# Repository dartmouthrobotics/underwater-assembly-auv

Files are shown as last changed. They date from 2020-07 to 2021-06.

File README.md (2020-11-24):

# Dartmouth Droplet AUV
Repository containing parts list and CAD files to retrofit a BlueROV2 for improved autonomous operation. The starting point would be a BlueROV2 heavy. A CAD file of the build is available [here](https://www.dropbox.com/s/99sjkslvtko1nd0/Electronics.igs?dl=0). Note that the front mounting plate is different than what is in that CAD file. I was experimenting with adding fans for camera cooling. What I use now in the robot is represented in the dxf file below.

The DXF files are usable as laser cutting patterns. The files `Electronics Tray Body.dxf`, `Electronics Tray Body.dxf`, and `rear electronics tray mount.dxf` are cut from 4.9mm delrin plastic from ponoko.com

The file `Camera Mount.dxf` is cut from 3.2mm black delrin from ponoko.

The file `FCU Mount.dxf` is cut from 2mm aerospace aluminum from send cut send.

The hardware for assembling the components comes from mcmaster-carr and allied electronics (for the mounting brackets). See the packing lists for both of those orders for details on the components.

# Electronics

ESCs: 2x DALRC rocket 50a from [here](https://www.getfpv.com/dalrc-rocket-50a-3-6s-blheli-32-4-in-1-esc.html). You also need another FCU to configure the ESCs. We use the DALRC f722 dual from [here](https://www.banggood.com/DALRC-F722-DUAL-STM32F722RGT6-F7-Flight-Controller-MPU6000-and-ICM20602-Built-in-OSD-for-RC-Drone-p-1346923.html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)

Main computer: UpBoard UpSquared [here](https://up-board.org/upsquared/specifications/). We use the 8GB ram quad core model
Main computer addons:
  * UpSquared wifi kit [here](https://up-shop.org/m-2-2230-wifi-kit-wifi-802-11-ac-2t2r-for-up-squared-metal-chassis.html) used to connect to the robot when it is on the surface
  * SSD for the upboard. We use [this one](https://www.amazon.com/gp/product/B07GZLJD5R/ref=ppx_yo_dt_b_search_asin_title?ie=UTF8&psc=1)
  * Tiny USB 2 cable for connecting to FCU [here](https://www.amazon.com/gp/product/B01NAMTC5T/ref=ppx_yo_dt_b_search_asin_title?ie=UTF8&psc=1)
  * Locking but small USB 3 cable for connecting to the camera [here](https://www.usbfirewire.com/parts/rr-armsk-xxgr.html#RR-ARMSK-12GR)
  
FCU: An Mrobotics X2.1. It is a smaller clone of the pixhawk with updated sensors. Available [here](https://store.mrobotics.io/mRo-X2-1-Rev-2-p/mro-x2.1rv2-mr.htm). We ordered with all cable options. Essential is the bridge cable for usb2.0 connection.

Power management:
  * Blue robotics underwater switch for the relay [here](https://bluerobotics.com/store/comm-control-power/switch/switch-10-5a-r1/)
  * 80A car relay. We used [this](https://www.amazon.com/gp/product/B00RX11KLW/ref=ppx_yo_dt_b_search_asin_title?ie=UTF8&psc=1)
  * 2x ZTW BECs [here](https://www.amazon.com/gp/product/B071CHGWRM/ref=ppx_yo_dt_b_search_asin_title?ie=UTF8&psc=1). One powers the FCU and the other the upboard
  * 60A boat fuse [here](https://www.amazon.com/gp/product/B0000AXYEO/ref=ppx_yo_dt_b_search_asin_title?ie=UTF8&psc=1). Protects against runaway loops in control or firmware causing components to burn out.
  * 2.1mm barrell connector for UpSquared [here](https://www.amazon.com/gp/product/B081TV7SQ7/ref=ppx_yo_dt_b_search_asin_title?ie=UTF8&psc=1)
  
Camera:
  * FLIR Blackfly S U3 Model: BFS-U3-16S2M-CS: 1.6 MP, 226 FPS, Sony IMX273, Mono [here](https://www.flir.com/products/blackfly-s-usb3/?model=BFS-U3-16S2M-CS)
  * Lense: Stardot technologies LEN 3.5mm CS [here](http://stardot.com/megapixel-lenses)

# Other hardware

The mounting hardware order from McMaster has most of what you need. In addition to that, you need:

* I use velcro straps rather than zip ties [here](https://www.amazon.com/gp/your-account/order-history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). The rectangular  holes on the mounting plate are designed to allow you to feed the velcro through the plate allowing you to mount custom payloads easily.
* Aluminum hex standoffs to accomodate for the longer body plate are needed. Four of [these](https://www.mcmaster.com/98952A108/) and two of [these](https://www.mcmaster.com/98952A118/)
* A pack of vibration damping standoffs for the FCU: [here](https://www.amazon.com/gp/product/B082ZNTKXT/ref=ppx_yo_dt_b_search_asin_image?ie=UTF8&psc=1)
* Vibration damping washers for mounting below the camera. I also put these washers between the thrusters and the vehicle's body: [here](https://www.amazon.com/gp/product/B077B5PPMQ/ref=ppx_yo_dt_b_search_asin_title?ie=UTF8&psc=1)
* 4 of steel corner brackets for mounting the camera plate: [here](https://www.alliedelec.com/product/keystone-electronics/4336/70181667/?referrer=search)
* For my current build, I use mr30 connectors to bridge between the ESC's output wires and the penetrators. I think it would be better to use regular bullet connectors instead of these though: [here](https://www.amazon.com/gp/product/B0711XJ3Q2/ref=ppx_yo_dt_b_search_asin_title?ie=UTF8&psc=1)
* Upgrading to the cobalt connector-ized thrusters was a big lifestyle improvement. I use the cobalt connectors whenever I can: https://www.bluetrailengineering.com/product-page/blue-robotics-t200-thruster-with-cobalt-connector
* I use high flexibility silicone wire everywhere inside the tube. It packs better than standard wire and is supposed to stand up better to vibration than standard wire. I used various sizes of this brand: [here](https://www.amazon.com/BNTECHGO-Silicone-Flexible-Resistant-Insulation/dp/B018H1BDP4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)

# Notes

* The ESC->penetrator connections are tough to fit in. You need to solder the ESC's wires at 90 degrees to the ESC body
* I use this brand of silica gel packet [here](https://www.amazon.com/gp/product/B01LZAQPEY/ref=ppx_yo_dt_b_search_asin_title?ie=UTF8&psc=1). Because of how warm it can get in the tube when the UpSquared is churning, silica descicant is necessary in the main electronics tube.
* The wifi setup I use as the virtual tether makes the upboard unable to connect to the internet. To make life easier I run one of [these](https://www.amazon.com/gp/product/B01IQWGKQ6/ref=ppx_yo_dt_b_search_asin_title?ie=UTF8&psc=1) ethernet cables into the camera compartment so I can easily jack the robot into the internet. I keep an ethernet cable with a junction like [this](https://www.amazon.com/gp/product/B016B13U9Y/ref=ppx_yo_dt_b_search_asin_title?ie=UTF8&psc=1) handy.
* If you want to run the robot with a tether, you will need to find a place to put the fathom-X board (the tether interface board) and to connect it to an ethernet jack on the UpBoard. There should be a good spot for doing this below the UpBoard's heatsink on the underside of the electronics board.

# Software setup

## TODO flesh this out

Install SimpleSub on the FCU. The source code for SimpleSub can be found here https://gitlab.com/dartmouthrobotics/ardupilot-simplesub. Instructions for building and uploading coming soon.

Install Ubuntu 18.04 server on the UpSquared, ensuring that it is booting from the SSD and not the EMMC memory that comes with the board. Install ROS melodic.

## Building & Installing the SimpleSub FCU firmware 

The FCU runs a custom built Ardupilot firmware that I call SimpleSub. SimpleSub can be found here: https://gitlab.com/dartmouthrobotics/ardupilot-simplesub/-/tree/SimpleSub-v0.0.1 

Clone that repository and ensure you are on the SimpleSub branch. Once you have done so, run the environment setup script that ardupilot provides by picking the right script from this directory for your OS https://gitlab.com/dartmouthrobotics/ardupilot-simplesub/-/tree/SimpleSub-v0.0.1/Tools/environment_install 

After that is done, you need to reload your environment: source ~/.bashrc (if on linux) 

With that, you should be able to build the code with the following commands from the ardupilot directory: 

./waf configure –board=mRoX21 

./waf build –targets=simplesub/SimpleSub 

Adding the –upload option onto the waf build command should upload the firmware to the FCU if the FCU is plugged in to your computer via a usb connection, but this doesn’t work for me. What works is running QGroundControl and then plugging the FCU into the computer and using that GUI to upload the custom firmware. The waf build command above will put a file called “simplesub.apj” into the “bin” folder. In the QGroundControl GUI, select the upload custom firmware option and select “simplesub.apj”. This should work! 

Another option for uploading the firmware that works for me is: 

./waf --upload --targets simplesub/SimpleSub --upload-port /dev/ttyACM0 (I found the device descriptor /dev/ttyACM0 by looking at dmesg) 

In addition it can be built and uploaded simultaneously like so: 

./waf build --upload --targets simplesub/SimpleSub --upload-port /dev/ttyACM0 

It looks like the issue with this was that when the device is rebooted by the firmware uploader script, it gets a different device id. The firmware uploader correctly found the first usb serial device (look at /dev/serial/by-id to find the one), but when it is booted in firmware mode, it got a different id. 

This command should be easier to replicate and it worked. The first usb serial device is the one that shows normally, and the second is the one after trying to run the firmware uploader: 

./waf build --upload --targets simplesub/SimpleSub --upload-port /dev/serial/by-id/usb-ArduPilot_mRoX21_3C001D000C51383437313533-if00,/dev/serial/by-id/usb-AUAV_PX4_BL_AUAV_X2.1_0-if00 

## Notes on setting up the wifi to allow remote wireless shell access

How to make the upboard an access point

1. Install isc-dhcp-server and hostapd

in file: /etc/hostapd/hostapd.conf add:

```
interface=wlan0
driver=nl80211
ssid=bluerov-network
hw_mode=g
channel=1
macaddr_acl=0
auth_algs=1
ignore_broadcast_ssid=0
wpa=3
wpa_passphrase=BlueROV2
wpa_key_mgmt=WPA-PSK
wpa_pairwise=TKIP
rsn_pairwise=CCMP
```

in file /etc/network/interfaces add:

```
# ifupdown has been replaced by netplan(5) on this system.  See
# /etc/netplan for current configuration.
# To re-enable ifupdown on this system, you can run:
#    sudo apt install ifupdown

auto wlan0
iface wlan0 inet static
	address 10.10.0.1
	netmask 255.255.255.0
```

in file /etc/dhcp/dhcpd.conf add:

```
authoritative;
log-facility local7;

subnet 10.10.0.0 netmask 255.255.255.0 {
	range 10.10.0.2 10.10.0.16;
	option domain-name-servers 8.8.8.8;
	option routers 10.10.0.1;
	option subnet-mask 255.255.255.0;
        option domain-name "testnet.local";
        option broadcast-address 10.10.0.255;
	default-lease-time 28800;
	max-lease-time 28800;
}
```

start hostapd:

```
sudo service hostapd start
```

give wlan0 an ip address:

```
sudo ifconfig wlan0 10.10.0.1 netmask 255.255.255.0
```

start isc-dhcp-server:

```
sudo service isc-dhcp-server start
```

Make sure to edit the file /etc/default/hostapd and set the DAEMON_CONF value

need also to "unmask" the hostapd service

```
sudo systemctl unmask hostapd
sudo systemctl enable hostapd
```

Also make sure to edit the INTERFACESV4 variable in /etc/default/isc-dhcp-server to include wlan0

It should be `INTERFACESV4="wlan0"` also the file should include `INTERFACES="wlan0"`

In /etc/rc.local do:

```
#! /bin/sh -e

service hostapd stop
service isc-dhcp-server stop
service hostapd start
ifconfig wlan0 192.168.2.2 netmask 255.255.255.0
service isc-dhcp-server start
```

To stop the upboard from lagging at boot when no network is connected, do 

```
systemctl disable systemd-networkd-wait-online.service
systemctl mask systemd-networkd-wait-online.service
```

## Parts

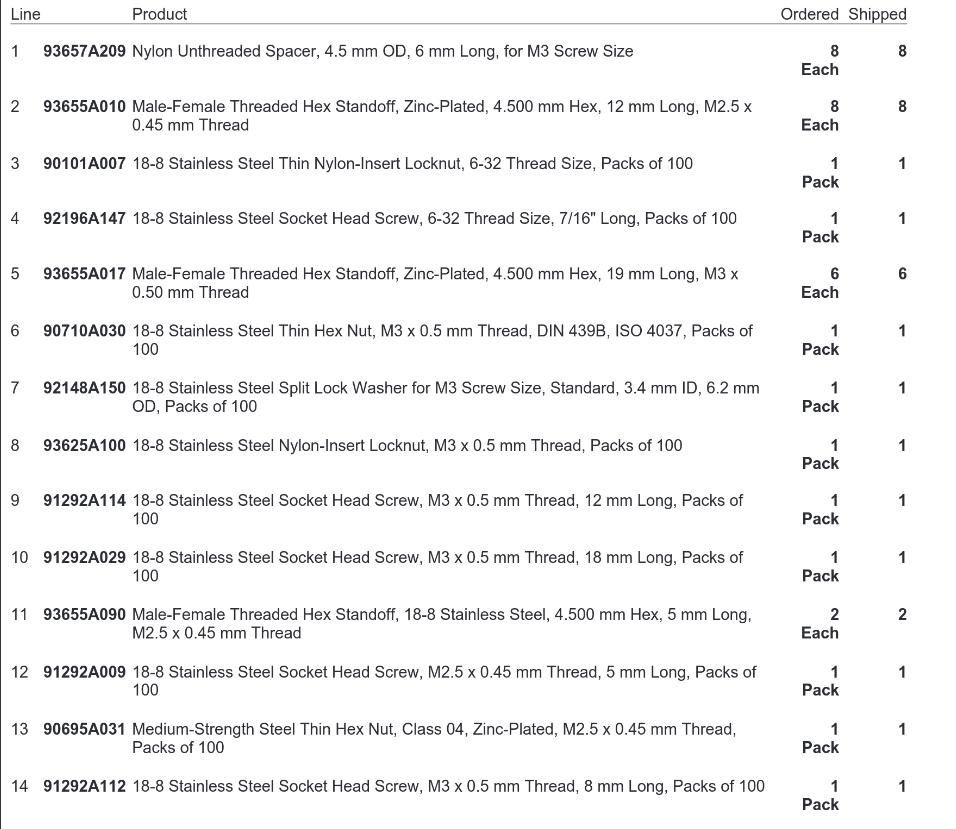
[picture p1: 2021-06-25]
parts-list-mcmaster.png

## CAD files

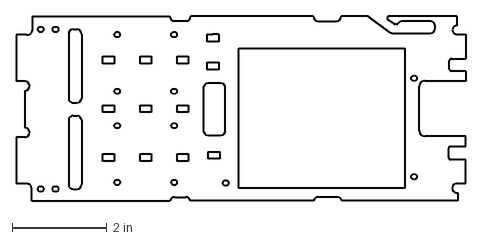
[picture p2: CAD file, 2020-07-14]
Electronics Tray Body.dxf
9.51 x 3.90 in

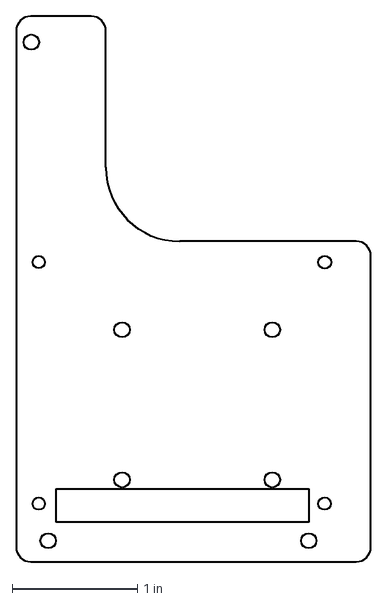
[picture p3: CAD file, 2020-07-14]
FCU Mount.dxf
2.83 x 4.36 in

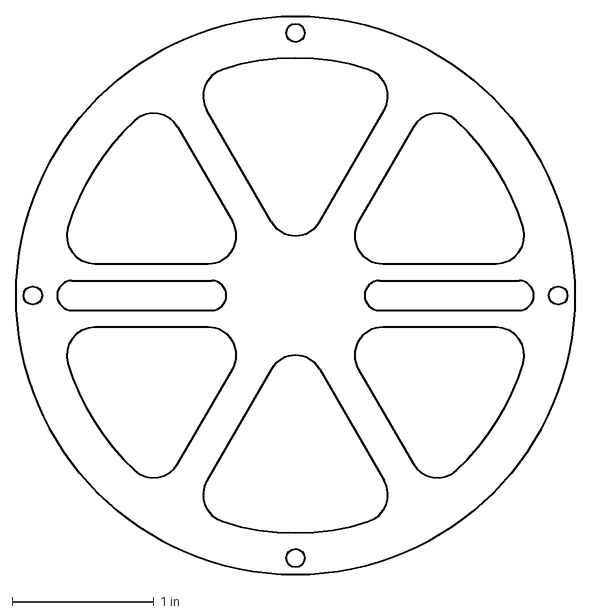
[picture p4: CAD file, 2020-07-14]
rear electronics tray mount.dxf
3.94 x 3.94 in

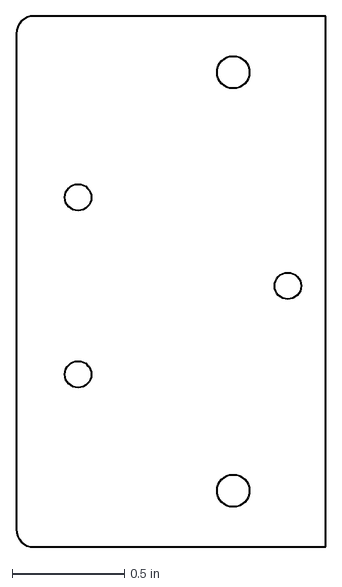
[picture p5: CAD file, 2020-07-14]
Camera Mount.dxf
1.38 x 2.36 in
